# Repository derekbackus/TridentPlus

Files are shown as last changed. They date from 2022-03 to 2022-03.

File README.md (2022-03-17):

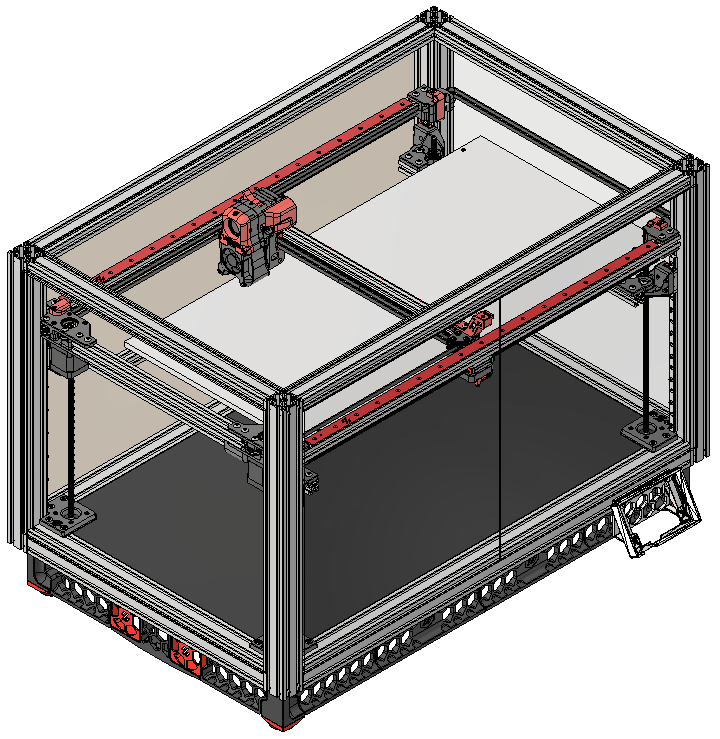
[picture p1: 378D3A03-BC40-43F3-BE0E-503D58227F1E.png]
Trident Plus

# TridentPlus
 350x650 Voron Trident
# Notes
This is an advanced build. Please don’t try this for your first build. It is not easy and takes some mechanical skills. 
- The lead screws on the two Z motors need to be cut.
- All of the extrusions were drilled in-house on a drill press — there are no stock numbers for pre-drilled extrusions provided. There are drill jigs provided in the STL folder.
- You need to tap the extrusions for blind joints. This is easy and goes fast with a hand drill, clamp, tapping fluid and a SHARP 5mm tap.
- Getting 2 build plates level and aligned well enough to do a Z_TILT_ADJUST is not easy. You must perfectly level your printer to make this work.
- Configuring Klipper is a bit more difficult than configuring a Trident. In particular, there are two SSRs for the two bed heaters, and an extra Z motor adding to the z_tilt configuration.
# 3D CAD
All of the custom files are in the STL folder. Everything else should be printed from the stock Trident. Here’s the 3D view in an online version for your viewing pleasure. https://autode.sk/3JmR1mI. I will get the STL file ready. You'll need these so you can see where all the holes in the extrusions need to be drilled.
# Goals
- Build a printer with a print size of approximately 350Y x 650X x 220Z.
- Re-use all Trident parts, where possible, so I don’t have to re-invent the wheel.
- Update Trident parts minimally, where needed.
# Ideas/Plans
- Use 4 integrated lead screw motors in each corner for the Z, reusing all the plastic Trident bed parts, including the MGN9 rails.
- Axis will be rotated 90 degrees. Looking from the front, the print size will be 650 wide (x) with the gantry open on the right.
- Corner posts and bottom base extrusions will be upgraded to 4040.
- The long axis (x) will be upgraded to MGN12 rails.
- Printer will be enclosed to print ABS.
- AL print bed will be 2 350mm magnabeds with 2 heaters on the bottom. 2 PEI WhamBam sheets will be used side-by-side for the print surface.
- Add 14ga or 16ga steel backers to X & Y extrusions for rigidity.
# Possible Issues
- Belts are approximately 2.5 meters. How will they work/stretch, etc? **Seems to be ok. Slightly more ringing, which can be taken care of with input shaper**
- Gantry is 20mm extrusion — is this rigid enough? Will MGN12 rails and backers make them rigid enough? **Yes, it is rigid enough. My bed mesh varies by .1964. This seems pretty good ovoer 650mm**
- How fast can it print? Hopefully 150mm(ish) **Prints great at 150mm perimeters, 60mm external perimeters and 35mm/s cubed volumetric for the rest with a Rapido hot end**
- Will the bed be too heavy for the steppers? **No, the steppers handle the bed with ease**
- Will the 20mm bed rails be rigid enough? **Yes**
# Mods Included
- Klicky
- .075 steel extrusion backers based on these https://github.com/VoronDesign/VoronUsers/tree/master/printer_mods/whoppingpochard/extrusion_backers
- Purge bucket/brush based on these https://github.com/VoronDesign/VoronUsers/tree/master/printer_mods/edwardyeeks/Decontaminator_Purge_Bucket_&_Nozzle_Scrubber
- Qty. 2 Nevermore 4 filters.
- Runout sensor

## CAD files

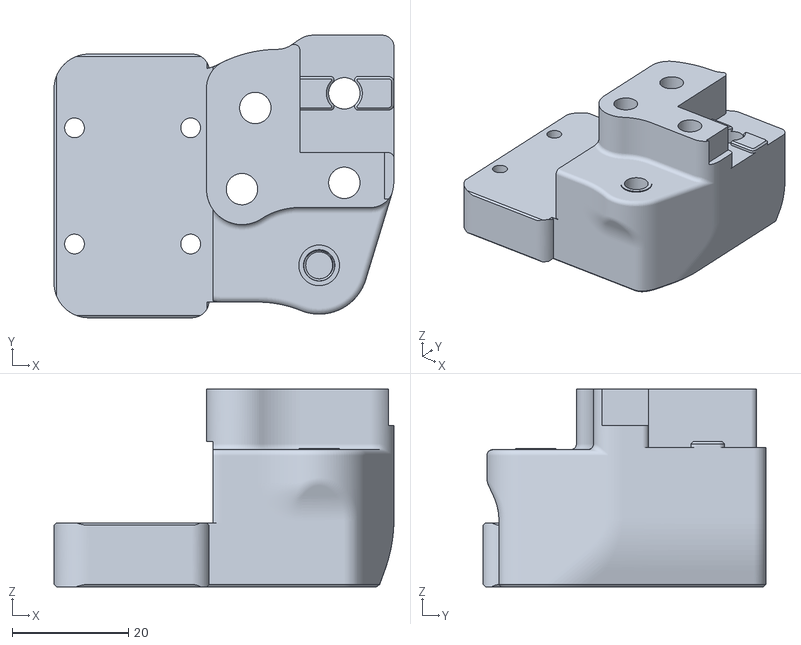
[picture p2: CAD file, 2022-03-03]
stl/Kiwi XY_Joint_Left_Lower.stl
58.5 x 48.6 x 34.0

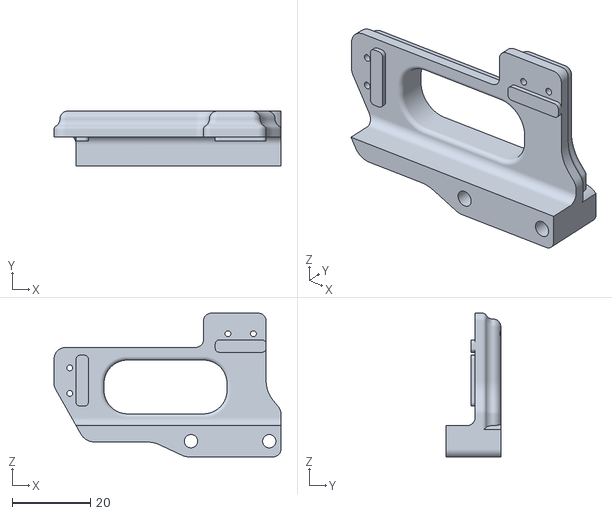
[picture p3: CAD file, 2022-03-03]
stl/Kiwi Endstop Pod.stl
58.0 x 14.0 x 36.7

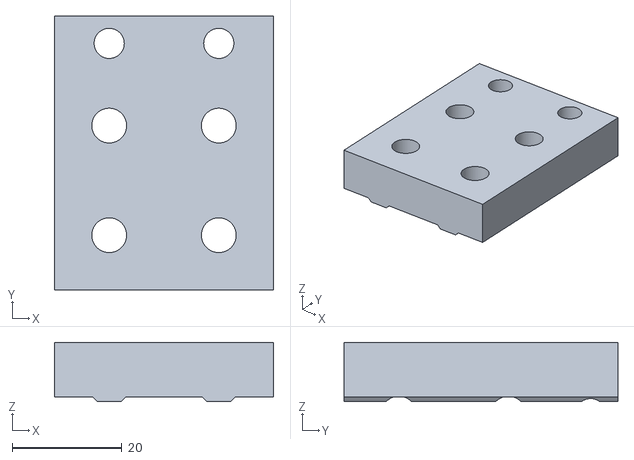
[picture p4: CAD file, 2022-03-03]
stl/4040 Drill Jig.stl
40.0 x 50.0 x 10.8

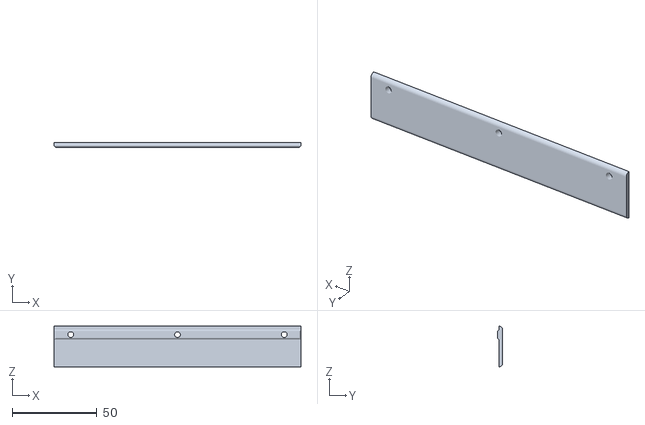
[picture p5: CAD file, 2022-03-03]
stl/Kiwi Bottom Cover Clips Sides Short.stl
145.8 x 3.00 x 24.0

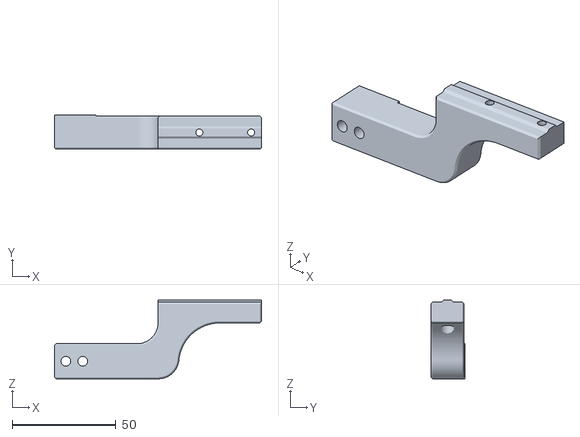
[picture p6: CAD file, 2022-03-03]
stl/Brush Holder.stl
100.0 x 16.5 x 38.0

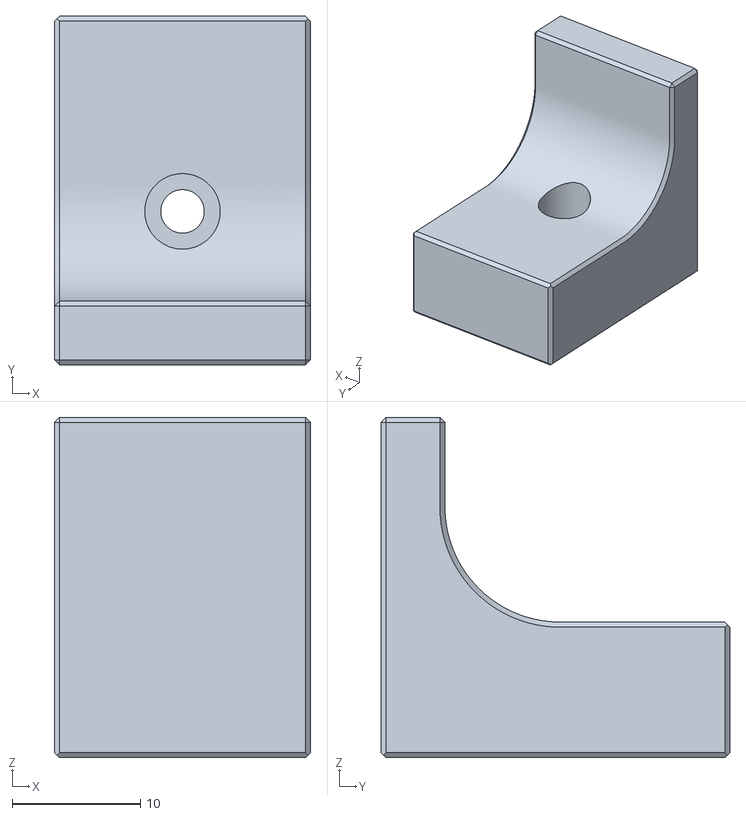
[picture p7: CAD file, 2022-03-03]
stl/Kiwi Y Endstop.stl
20.0 x 27.3 x 26.6

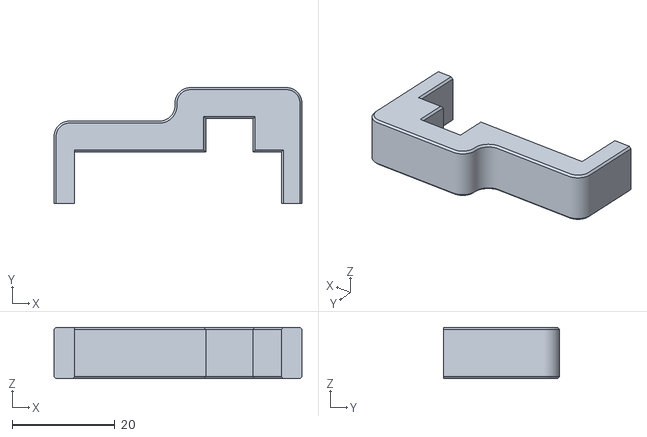
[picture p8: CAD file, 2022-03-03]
stl/MGN9 4040 Rail Guide.stl
48.2 x 22.5 x 10.0

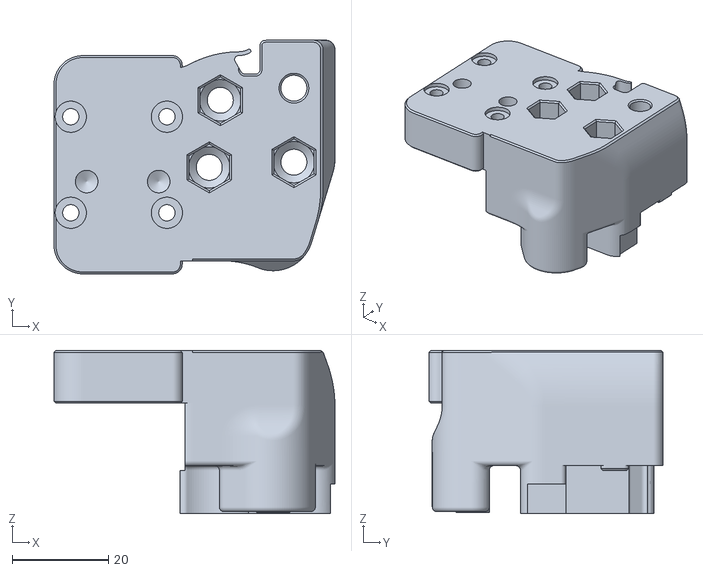
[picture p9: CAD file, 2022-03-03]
stl/Kiwi XY_Joint_Right_Lower.stl
58.5 x 48.7 x 34.0

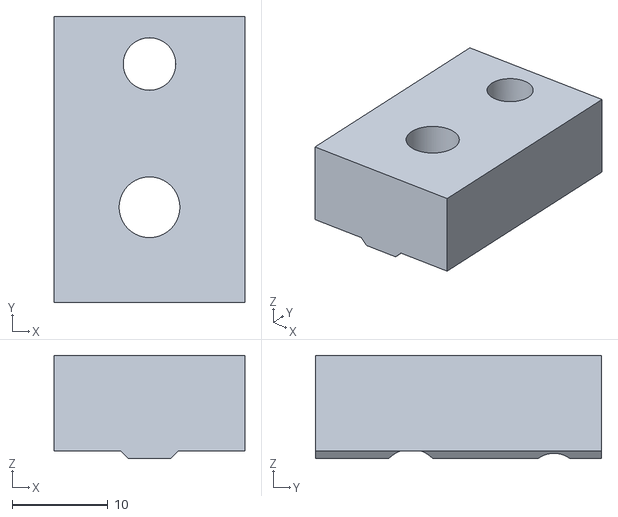
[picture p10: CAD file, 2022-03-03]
stl/2020 Drill Jig.stl
20.0 x 30.0 x 10.8

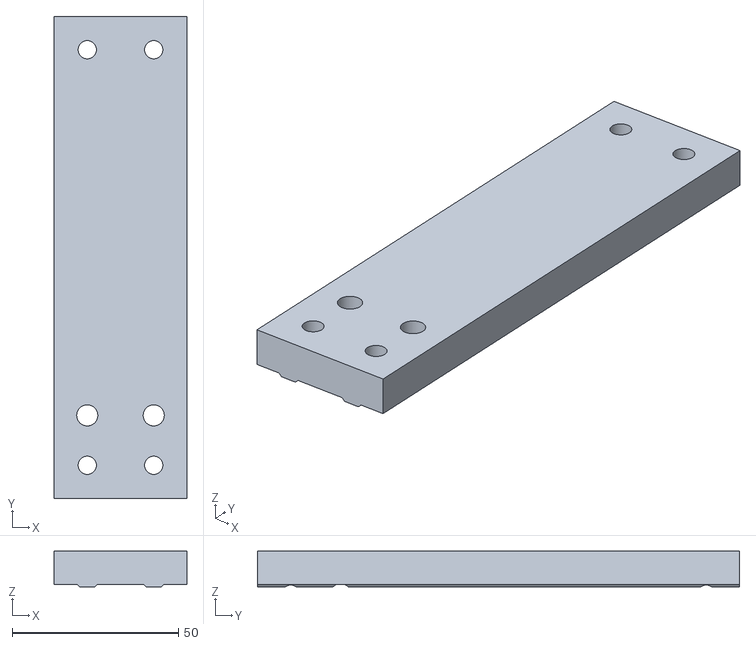
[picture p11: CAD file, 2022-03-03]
stl/4040-Mid Drill Jig.stl
40.0 x 145.0 x 10.8

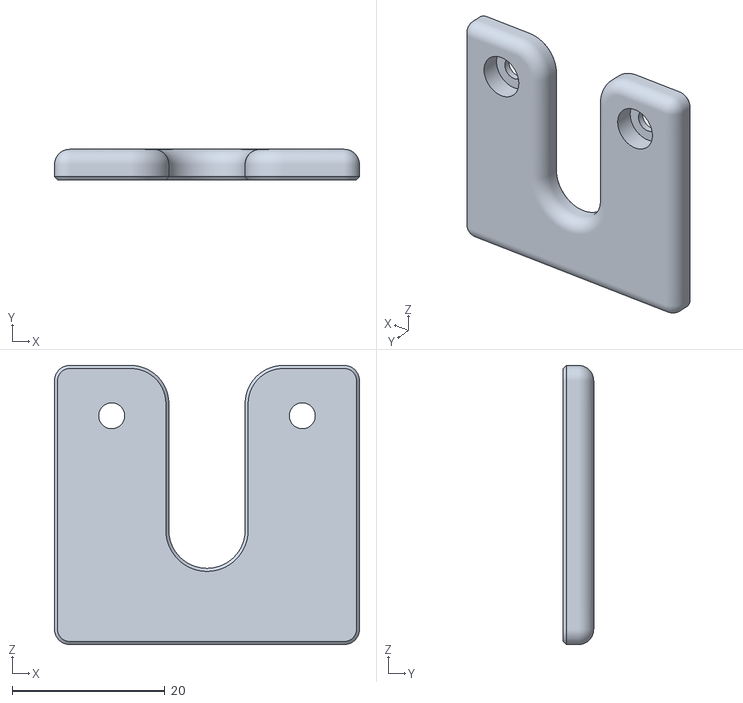
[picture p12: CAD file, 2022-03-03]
stl/Kiwi Bottom Wire Plate.stl
40.0 x 4.00 x 36.6

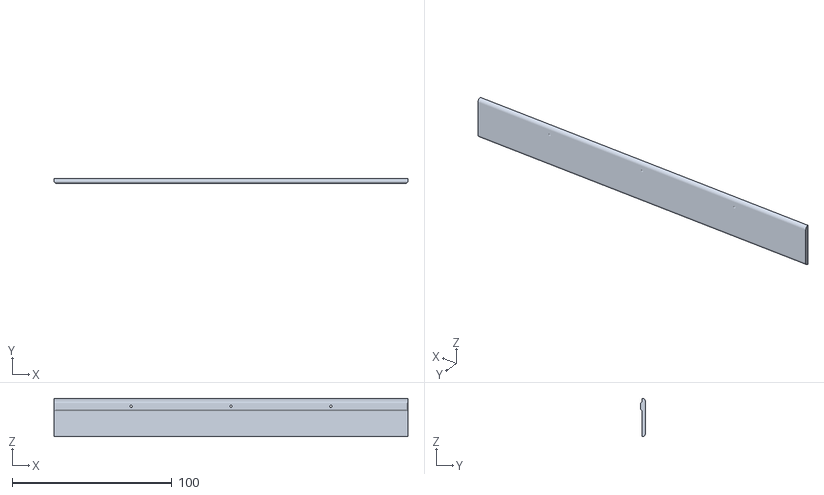
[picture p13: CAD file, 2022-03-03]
stl/Kiwi Bottom Cover Clips.stl
221.5 x 3.00 x 24.0

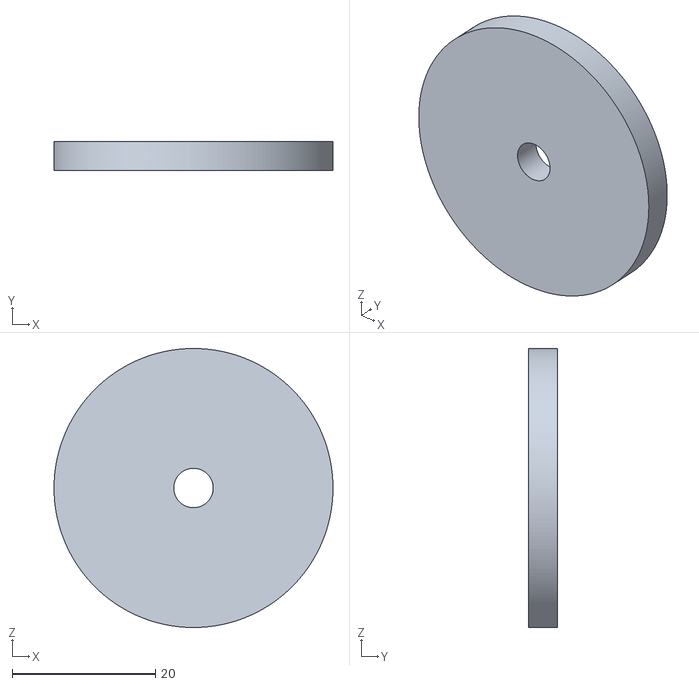
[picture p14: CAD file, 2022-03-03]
stl/Foot Spacer.stl
39.0 x 4.00 x 39.0

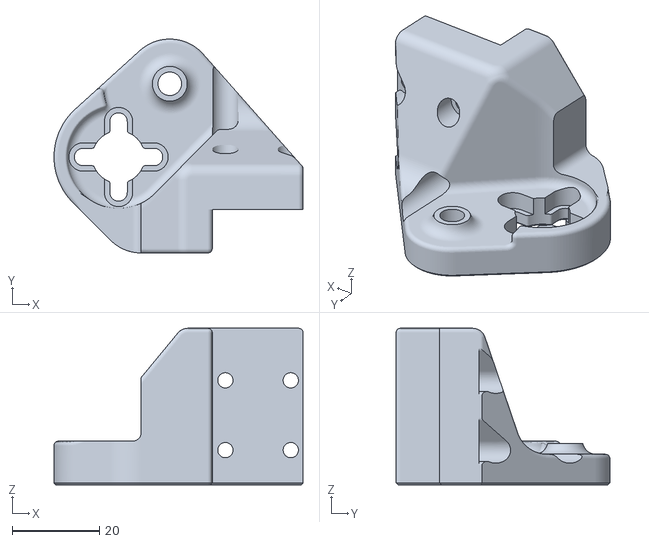
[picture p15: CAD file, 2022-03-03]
stl/Kiwi_Z_Carriage_Right.stl
57.1 x 49.1 x 35.9

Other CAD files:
stl/Gantry Spacer.stl
stl/Panel Mount.stl
stl/Kiwi_Z_Carriage_Left.stl
stl/Bed Chain Mount.stl
stl/Kiwi Bottom Cover Clips Sides.stl
stl/Middle Side Skirt.stl
stl/Switch Skirt.stl
